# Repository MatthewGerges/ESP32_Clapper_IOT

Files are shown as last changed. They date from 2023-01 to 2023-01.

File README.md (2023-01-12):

# ESP32 Clapper Light - an IOT Project

 Video demo: https://www.youtube.com/watch?v=oGSny03s_TQ


- This project consists of an ESP32 microcontroller (programmed in C++)  that flips a light switch in 0.2 seconds upon detecting 2 claps
- I implemented it to an IOT framework by connecting it to a MongoDB database managed by NodeJS on the backend. The ESP32 will query for changes to the database every 0.5 seconds
- This project will soon have a React Native front end as well
- I also created a PCB that manages all the connections to the ESP32 and allows the circuit to be powered in 3 different ways (via a USB connection, a 3.7V battery connected to a boost converter that increases the voltage to 5V, and through a 12V DC barrel jack ran through a LM7805 converter with 2 capacitors to manage power ripples)
- The PCB was taken from start to finish - I did the schematic design - bought the parts off of digikey after creating a BOM and had it manufactured at JLC PCB after comparing pricing and quality of other PCB manufacturers
- Cases, enclosures and extensions were also created for this project on Fusion360 and printed on my personal Ender 3 V2 Printer (which took several iterations and rounds of prototyping)
 


This repo contains 4 folders: 
1) The ESP32 code written in C++
2) The backend code written in NodeJS which uses an MVC (model-view-controller) framework and will be connected to the front end of a React-Native app that is on the way of being built
3) The PCB designs - including all the files needed for manufacturing the PCB. It was created on Altium CircuitMaker. As such all the design documents can be viewed here: https://365.altium.com/files/E79B46BD-EABC-40B6-B3DB-7410488752D2
4) The Fusion360 3D designs (containing f3d - fusion360 design files- and STL files used to print the designs on my ender-3-V2 printer). These include several iterations of the PCB case, the servo motor extension and the pentagon-shaped knob extender for the light switch.

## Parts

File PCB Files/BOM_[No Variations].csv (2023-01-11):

Comment | Description | Designator | Footprint | LibRef | Quantity
TP4056 | Lithium Battery Charger |  | TP4056-Footprint-1 | CMP-88poo8h67ic0nqpqrd41-1 | 1
Battery Holder 18650 | Pcb Holder Thm 18650 Polarized | BT1 | PCB-nmv0vzhkfwsbxqx6kc1g-1 | CMP-40d98835f05c9f1e-4 | 1
Würth Elektronik 860010372006 | Aluminium Electrolytic Capacitor, WCAP-ATG8 Series, 100 F, 20%, 16 V, 5 mm, Radial Leaded | C1 | CAP-5x11-2 | CMP-7bd7b1e54b20a410-1 | 1
Würth Elektronik 860020374012 | Al Electrolytic Capacitors 470uF 16V | C2 | PCB-3azp1z6rt2bm1haulf0v-1 | CMP-e25928656d7f3d9e-1 | 1
DC Jack 5.5 2.1 | Conn; AV; Power; Jack; Mini; 2.0mmPinDia; RtAngle; Thru-hole; forS760, S765Plug | J1 | PCB-gxnxm3n04w37egsept5y-1 | CMP-da391331d91005fe-17 | 1
Sound Sensor HRS-1B-03-GA | Pin header, single-row 90° 3-pin [JST] S3B-XH-A Pin header, single-row 90° 3-pin | S1 | PCB-2zo40p8xruutr4eka9s5-1 | CMP-45008c3683009ac7-6 | 1
ServoMotor G800W305018EU | Pin header, single-row 90° 3-pin [JST] S3B-XH-A Pin header, single-row 90° 3-pin | S2 | PCB-2zo40p8xruutr4eka9s5-1 | CMP-45008c3683009ac7-6 | 1
Boost Converter | Pin header, single-row 90° 3-pin [JST] S3B-XH-A Pin header, single-row 90° 3-pin | S3 | PCB-2zo40p8xruutr4eka9s5-1 | CMP-45008c3683009ac7-6 | 1
E-Switch EG1218 | Slide Switch, 500 V, -20 to 70 degC, 3-Pin THD, RoHS | SW1 | ESWI-EG1218_V | CMP-9a5a5340a2f5459d-9 | 1
LM7805CT/NOPB | Linear Voltage Regulators 5 Volt Reg [Texas Instruments] | U1 | PCB-m217x3dwscnnq8k6ksmn-1 | CMP-8a9e42f854f65559-10 | 1
Espressif Systems ESP32-DEVKITC-32D with header | Eval Board For ESP-WROOM-32 - 38pin module with 8.4mm header | U2 | PCB-v7o6mlcnvy9ltvisia1k-2 | CMP-0991c5192c5ed656-39 | 1

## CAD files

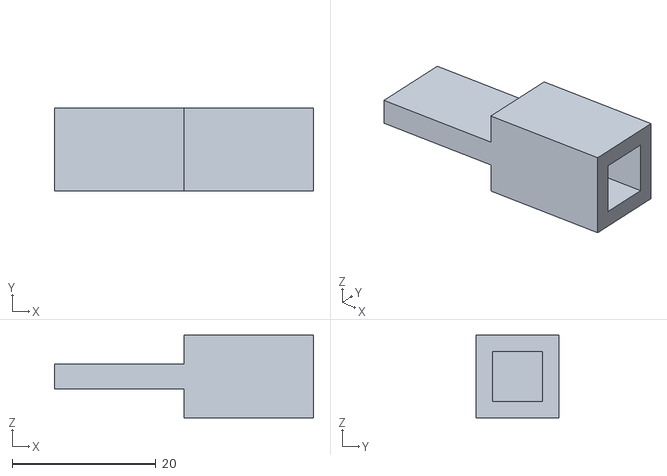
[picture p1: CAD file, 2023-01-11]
3D Design Files (Fusion360)/3D Print Files (STL)/KnobExt2_Brim.stl
36.0 x 11.5 x 11.5

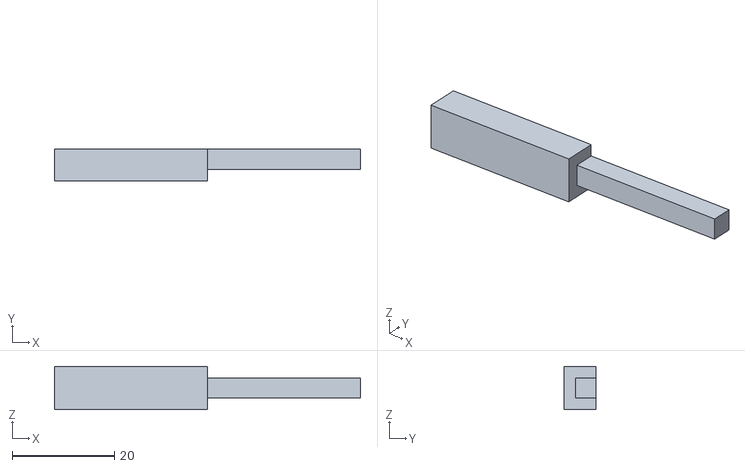
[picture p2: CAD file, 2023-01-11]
3D Design Files (Fusion360)/3D Print Files (STL)/ServoExtensionStraight_v2.stl
60.0 x 6.25 x 8.50

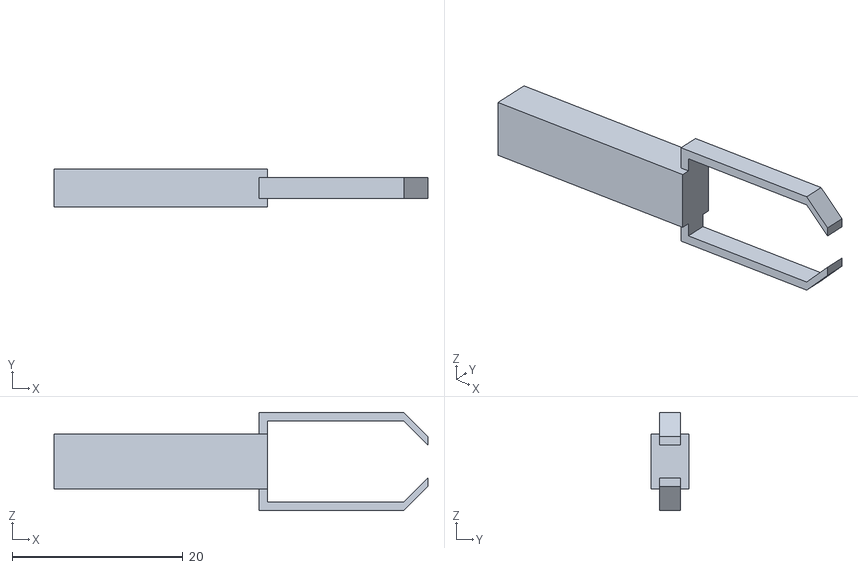
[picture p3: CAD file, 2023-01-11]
3D Design Files (Fusion360)/3D Print Files (STL)/Extension1.stl
43.8 x 4.50 x 11.5

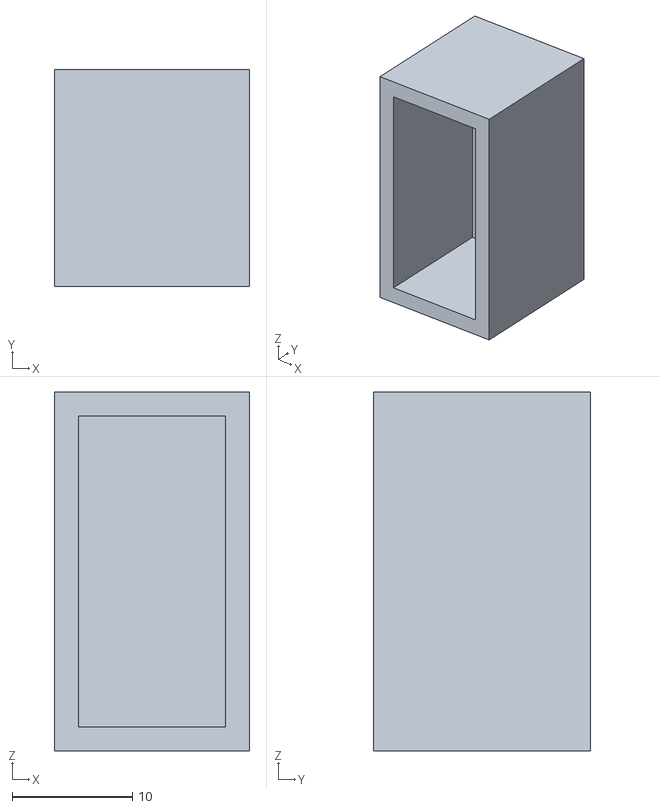
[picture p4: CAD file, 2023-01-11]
3D Design Files (Fusion360)/3D Print Files (STL)/ServoEncolosure2.stl
16.2 x 18.0 x 29.8

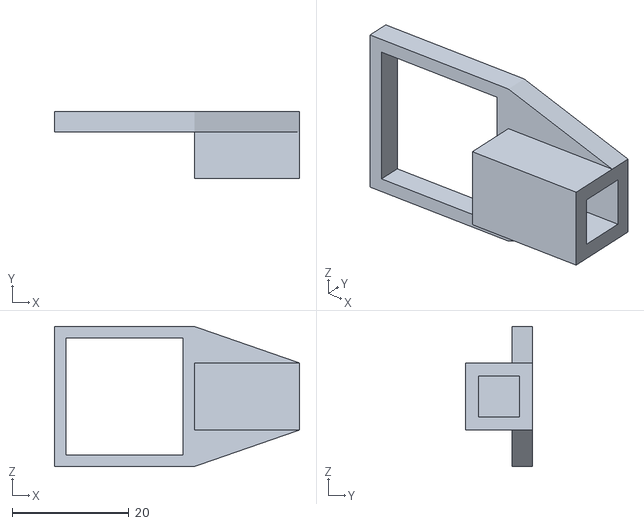
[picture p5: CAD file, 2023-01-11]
3D Design Files (Fusion360)/3D Print Files (STL)/KnobExtenderPentagon.stl
42.0 x 11.5 x 24.0

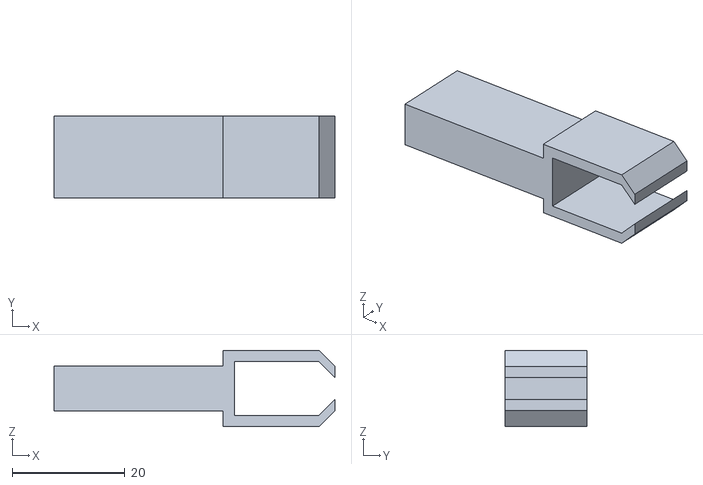
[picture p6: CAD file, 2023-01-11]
3D Design Files (Fusion360)/3D Print Files (STL)/Extension2.stl
49.8 x 14.5 x 13.5

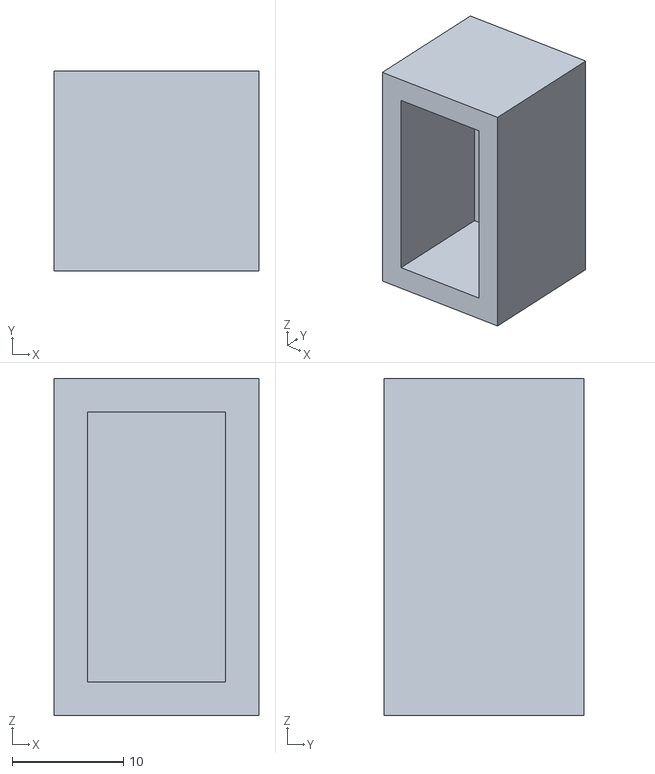
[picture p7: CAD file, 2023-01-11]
3D Design Files (Fusion360)/3D Print Files (STL)/ServoEncolosure1.stl
18.4 x 18.0 x 30.3

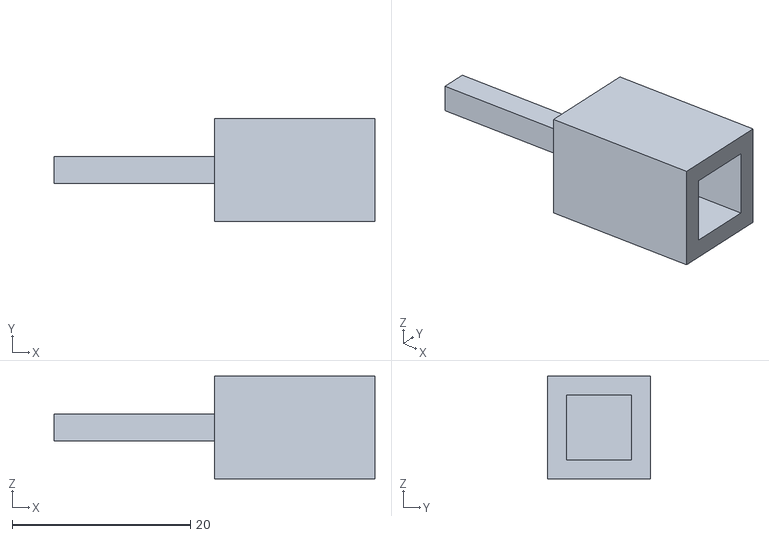
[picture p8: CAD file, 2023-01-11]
3D Design Files (Fusion360)/3D Print Files (STL)/KnobExtender1.stl
36.0 x 11.5 x 11.5

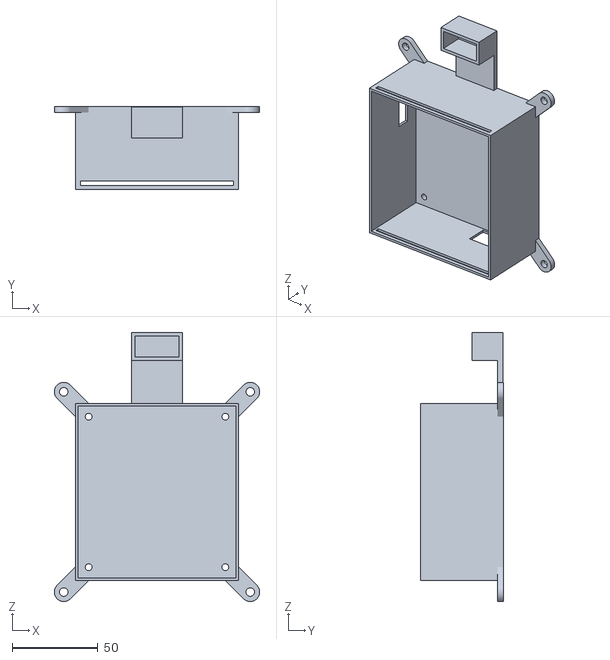
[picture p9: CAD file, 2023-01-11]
3D Design Files (Fusion360)/3D Print Files (STL)/PCBCase_v2_Slots.stl
119.5 x 48.5 x 156.4

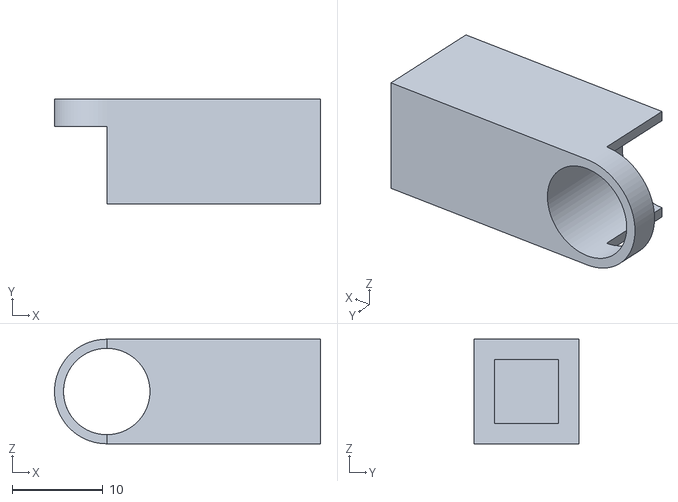
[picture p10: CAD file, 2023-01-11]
3D Design Files (Fusion360)/3D Print Files (STL)/KnobExtenderCircle.stl
29.2 x 11.5 x 11.5

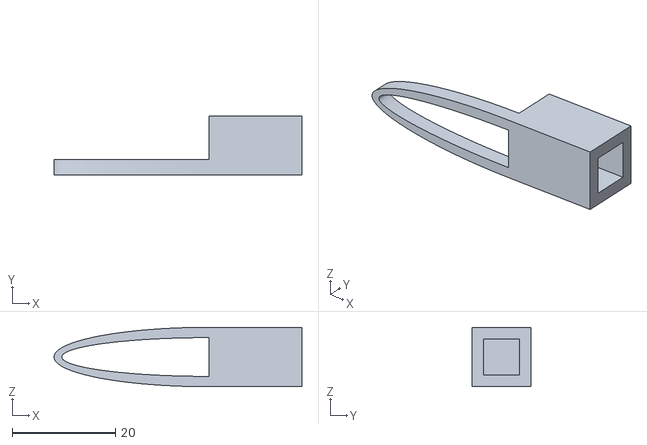
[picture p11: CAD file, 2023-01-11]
3D Design Files (Fusion360)/3D Print Files (STL)/KnobExtenderElipse.stl
48.0 x 11.5 x 11.5

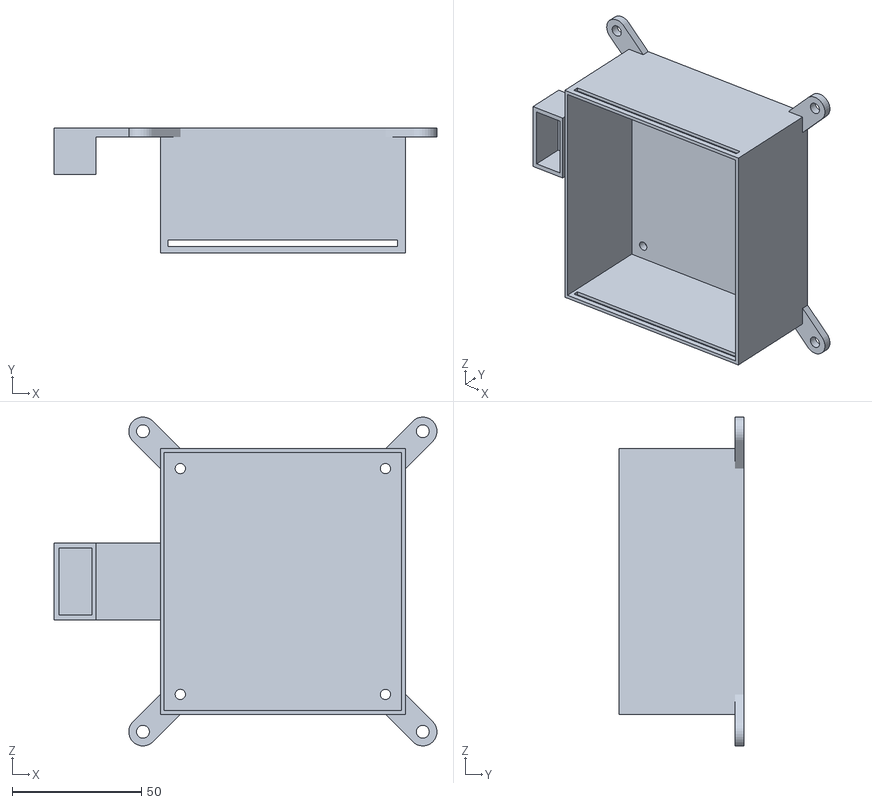
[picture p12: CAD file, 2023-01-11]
3D Design Files (Fusion360)/3D Print Files (STL)/PCBCase_v1_All.stl
148.4 x 48.5 x 127.5

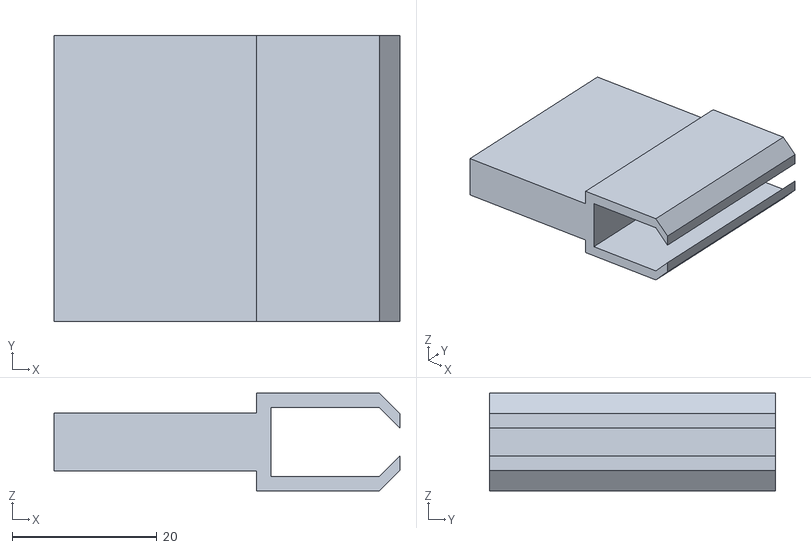
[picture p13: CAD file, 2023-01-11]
3D Design Files (Fusion360)/3D Print Files (STL)/Extension3.stl
47.8 x 39.5 x 13.5

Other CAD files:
3D Design Files (Fusion360)/3D Print Files (STL)/knobExtenderPentagon_2.stl
3D Design Files (Fusion360)/3D Print Files (STL)/PCBCase_v3_Aligned.stl
3D Design Files (Fusion360)/3D Print Files (STL)/ServoExtensionStraight.stl
3D Design Files (Fusion360)/Fusion360 Files (f3d)/LightKnobExtender.f3d
3D Design Files (Fusion360)/Fusion360 Files (f3d)/LightSwitcher.f3d
3D Design Files (Fusion360)/Fusion360 Files (f3d)/LightSwitcherStraight.f3d
3D Design Files (Fusion360)/Fusion360 Files (f3d)/PCBCase.f3d
3D Design Files (Fusion360)/Fusion360 Files (f3d)/ServoMotorEnclosure.f3d

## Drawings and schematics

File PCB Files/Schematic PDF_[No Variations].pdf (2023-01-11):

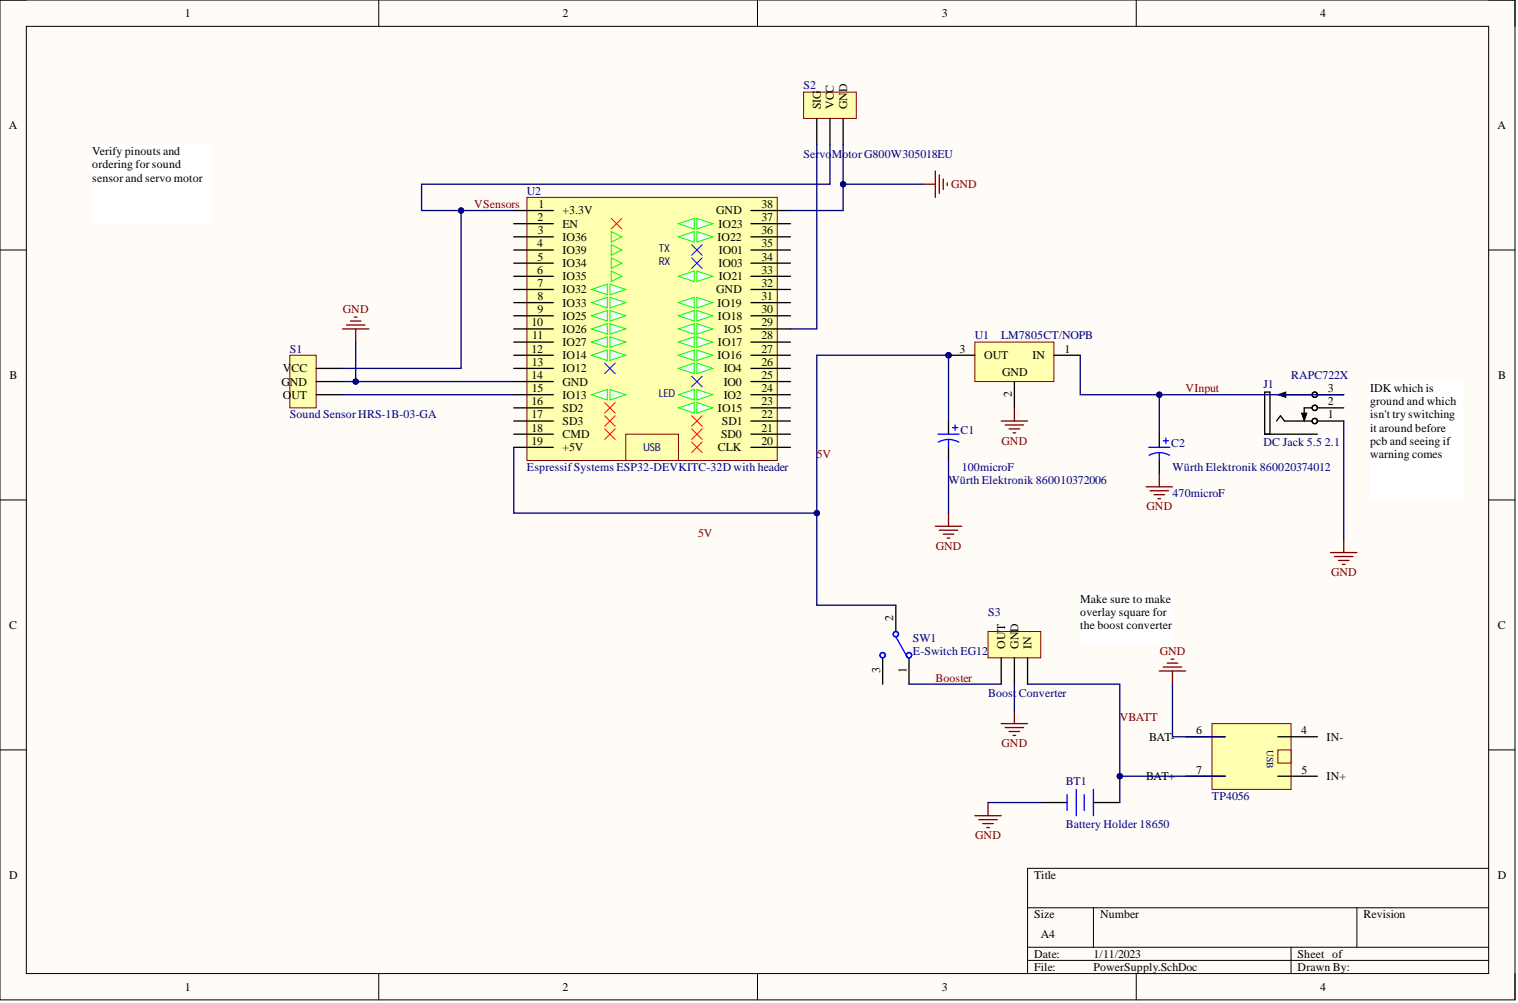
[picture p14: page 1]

Verify pinouts and
ordering for sound
sensor and servo motor

IDK which is
ground and which
isn't try switching
it around before
pcb and seeing if
warning comes

Espressif Systems ESP32-DEVKITC-32D with header

Make sure to make
overlay square for
the boost converter

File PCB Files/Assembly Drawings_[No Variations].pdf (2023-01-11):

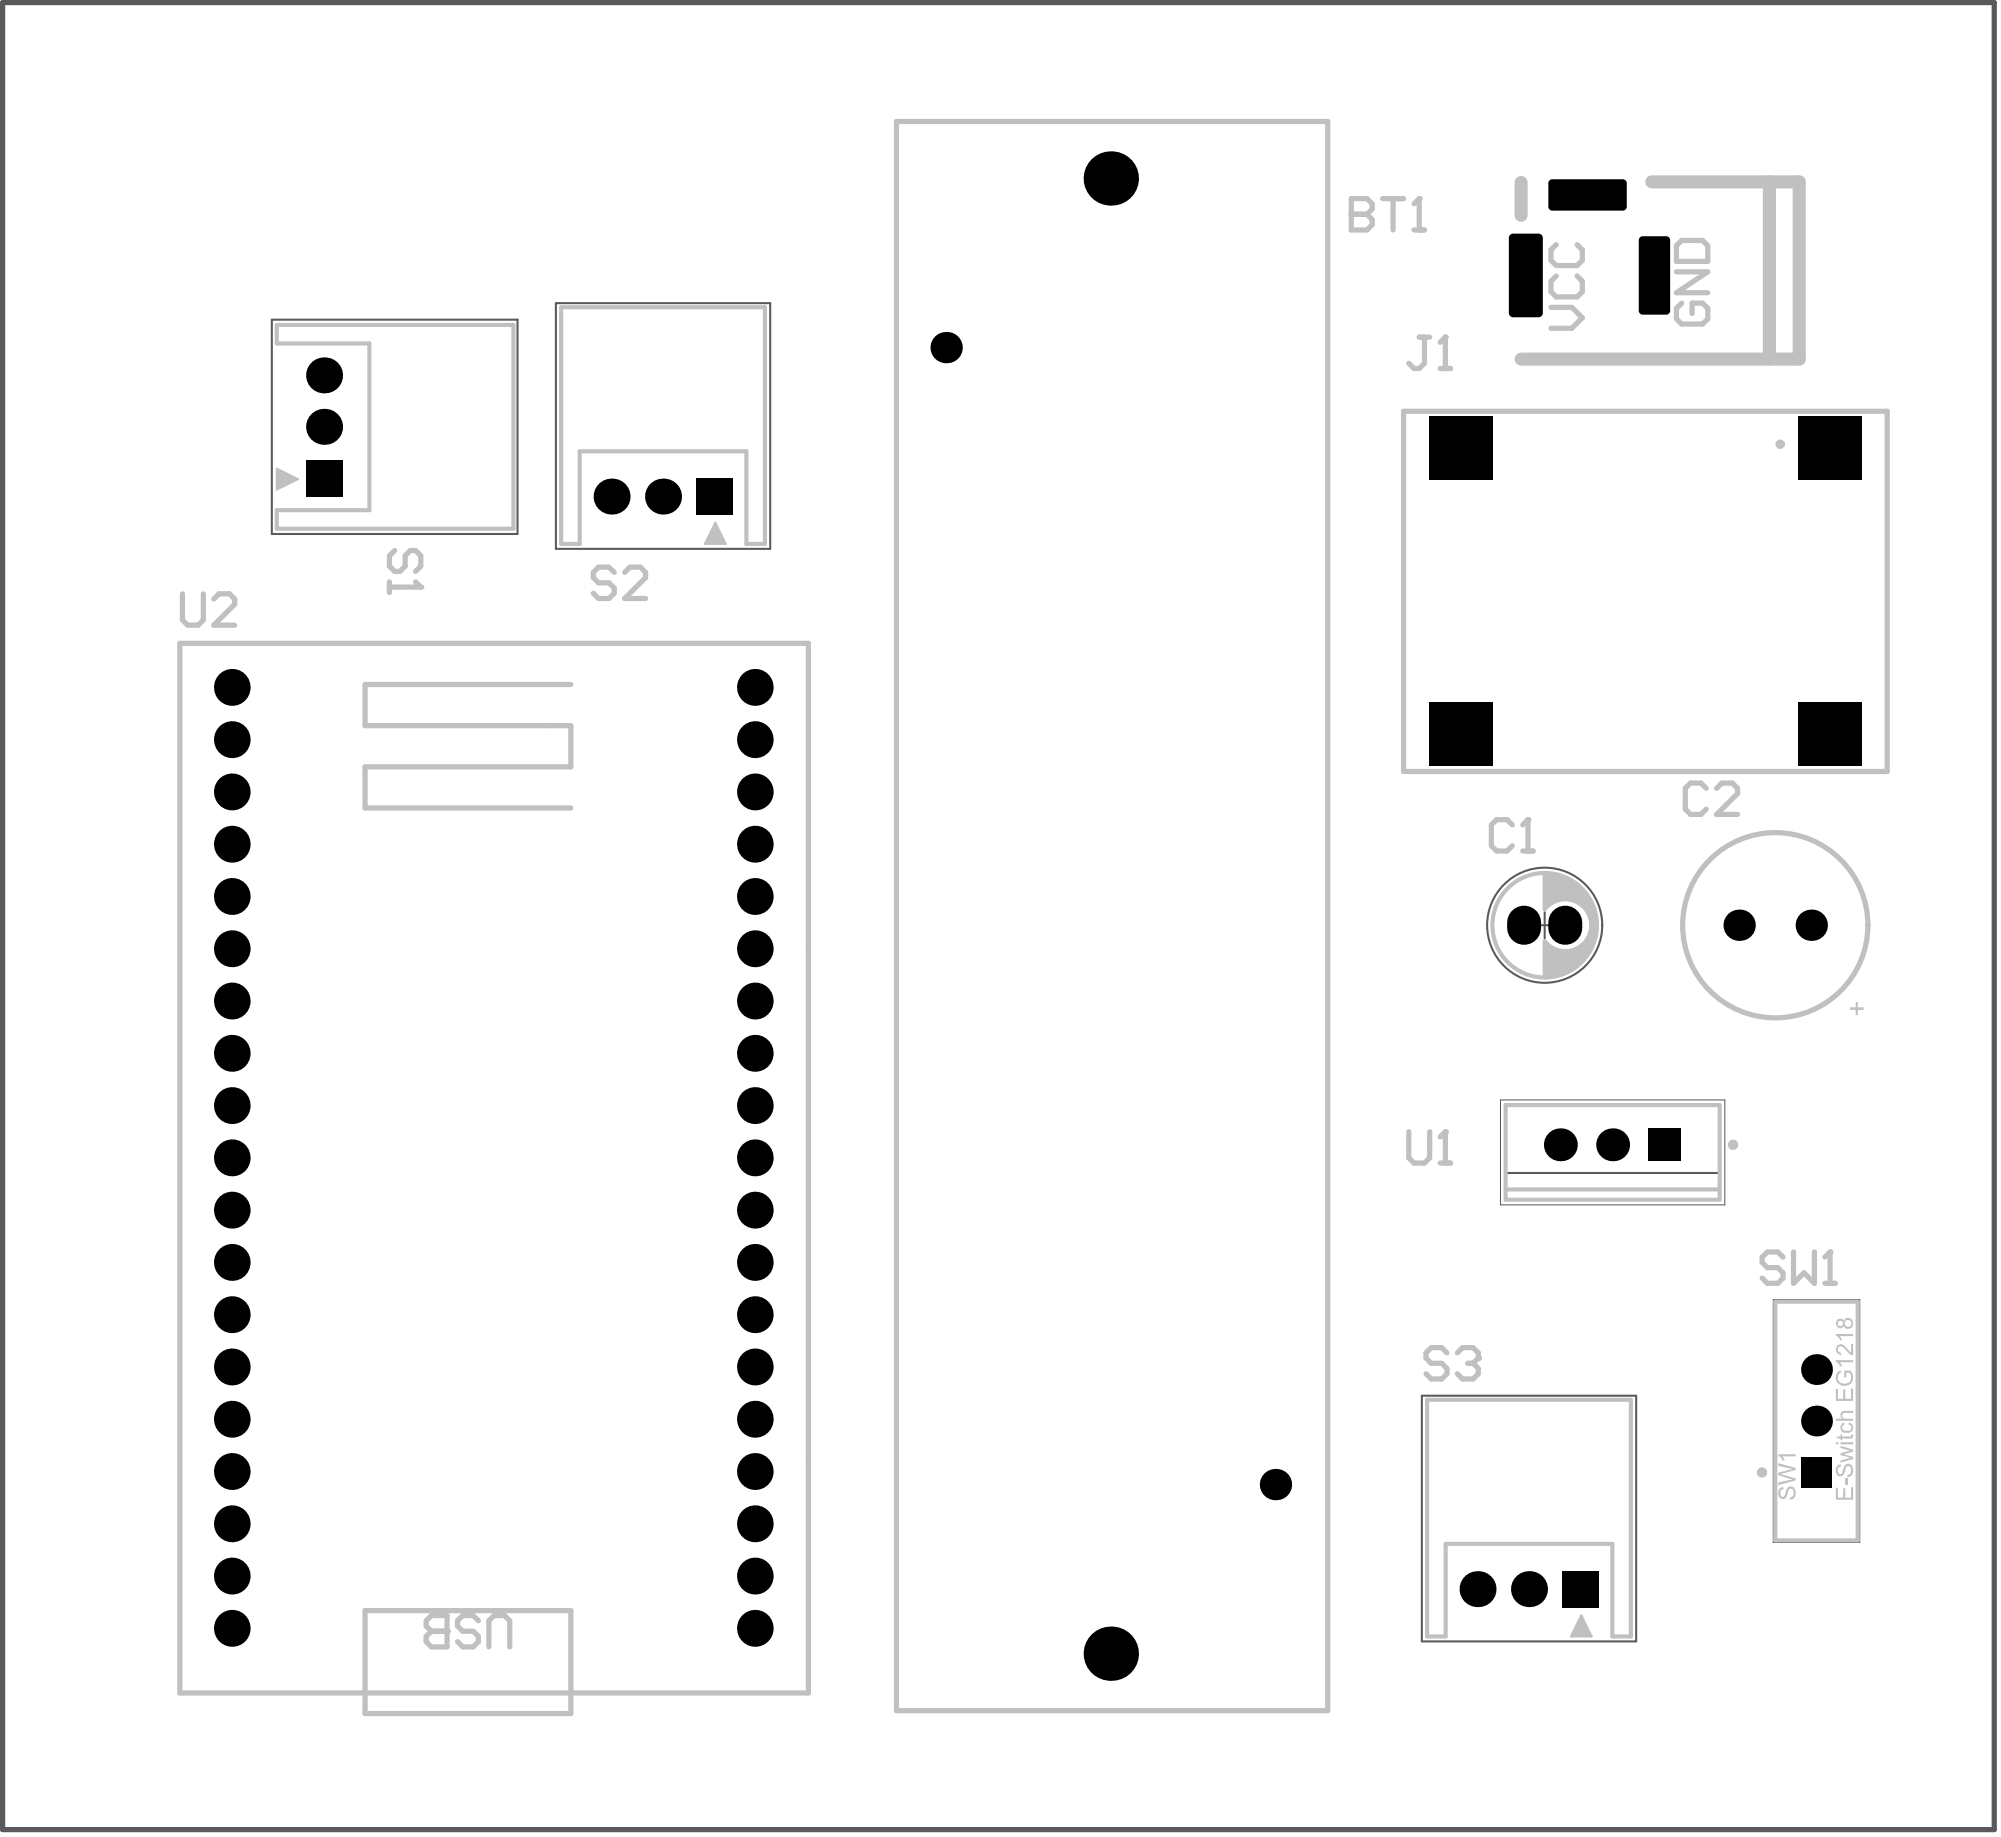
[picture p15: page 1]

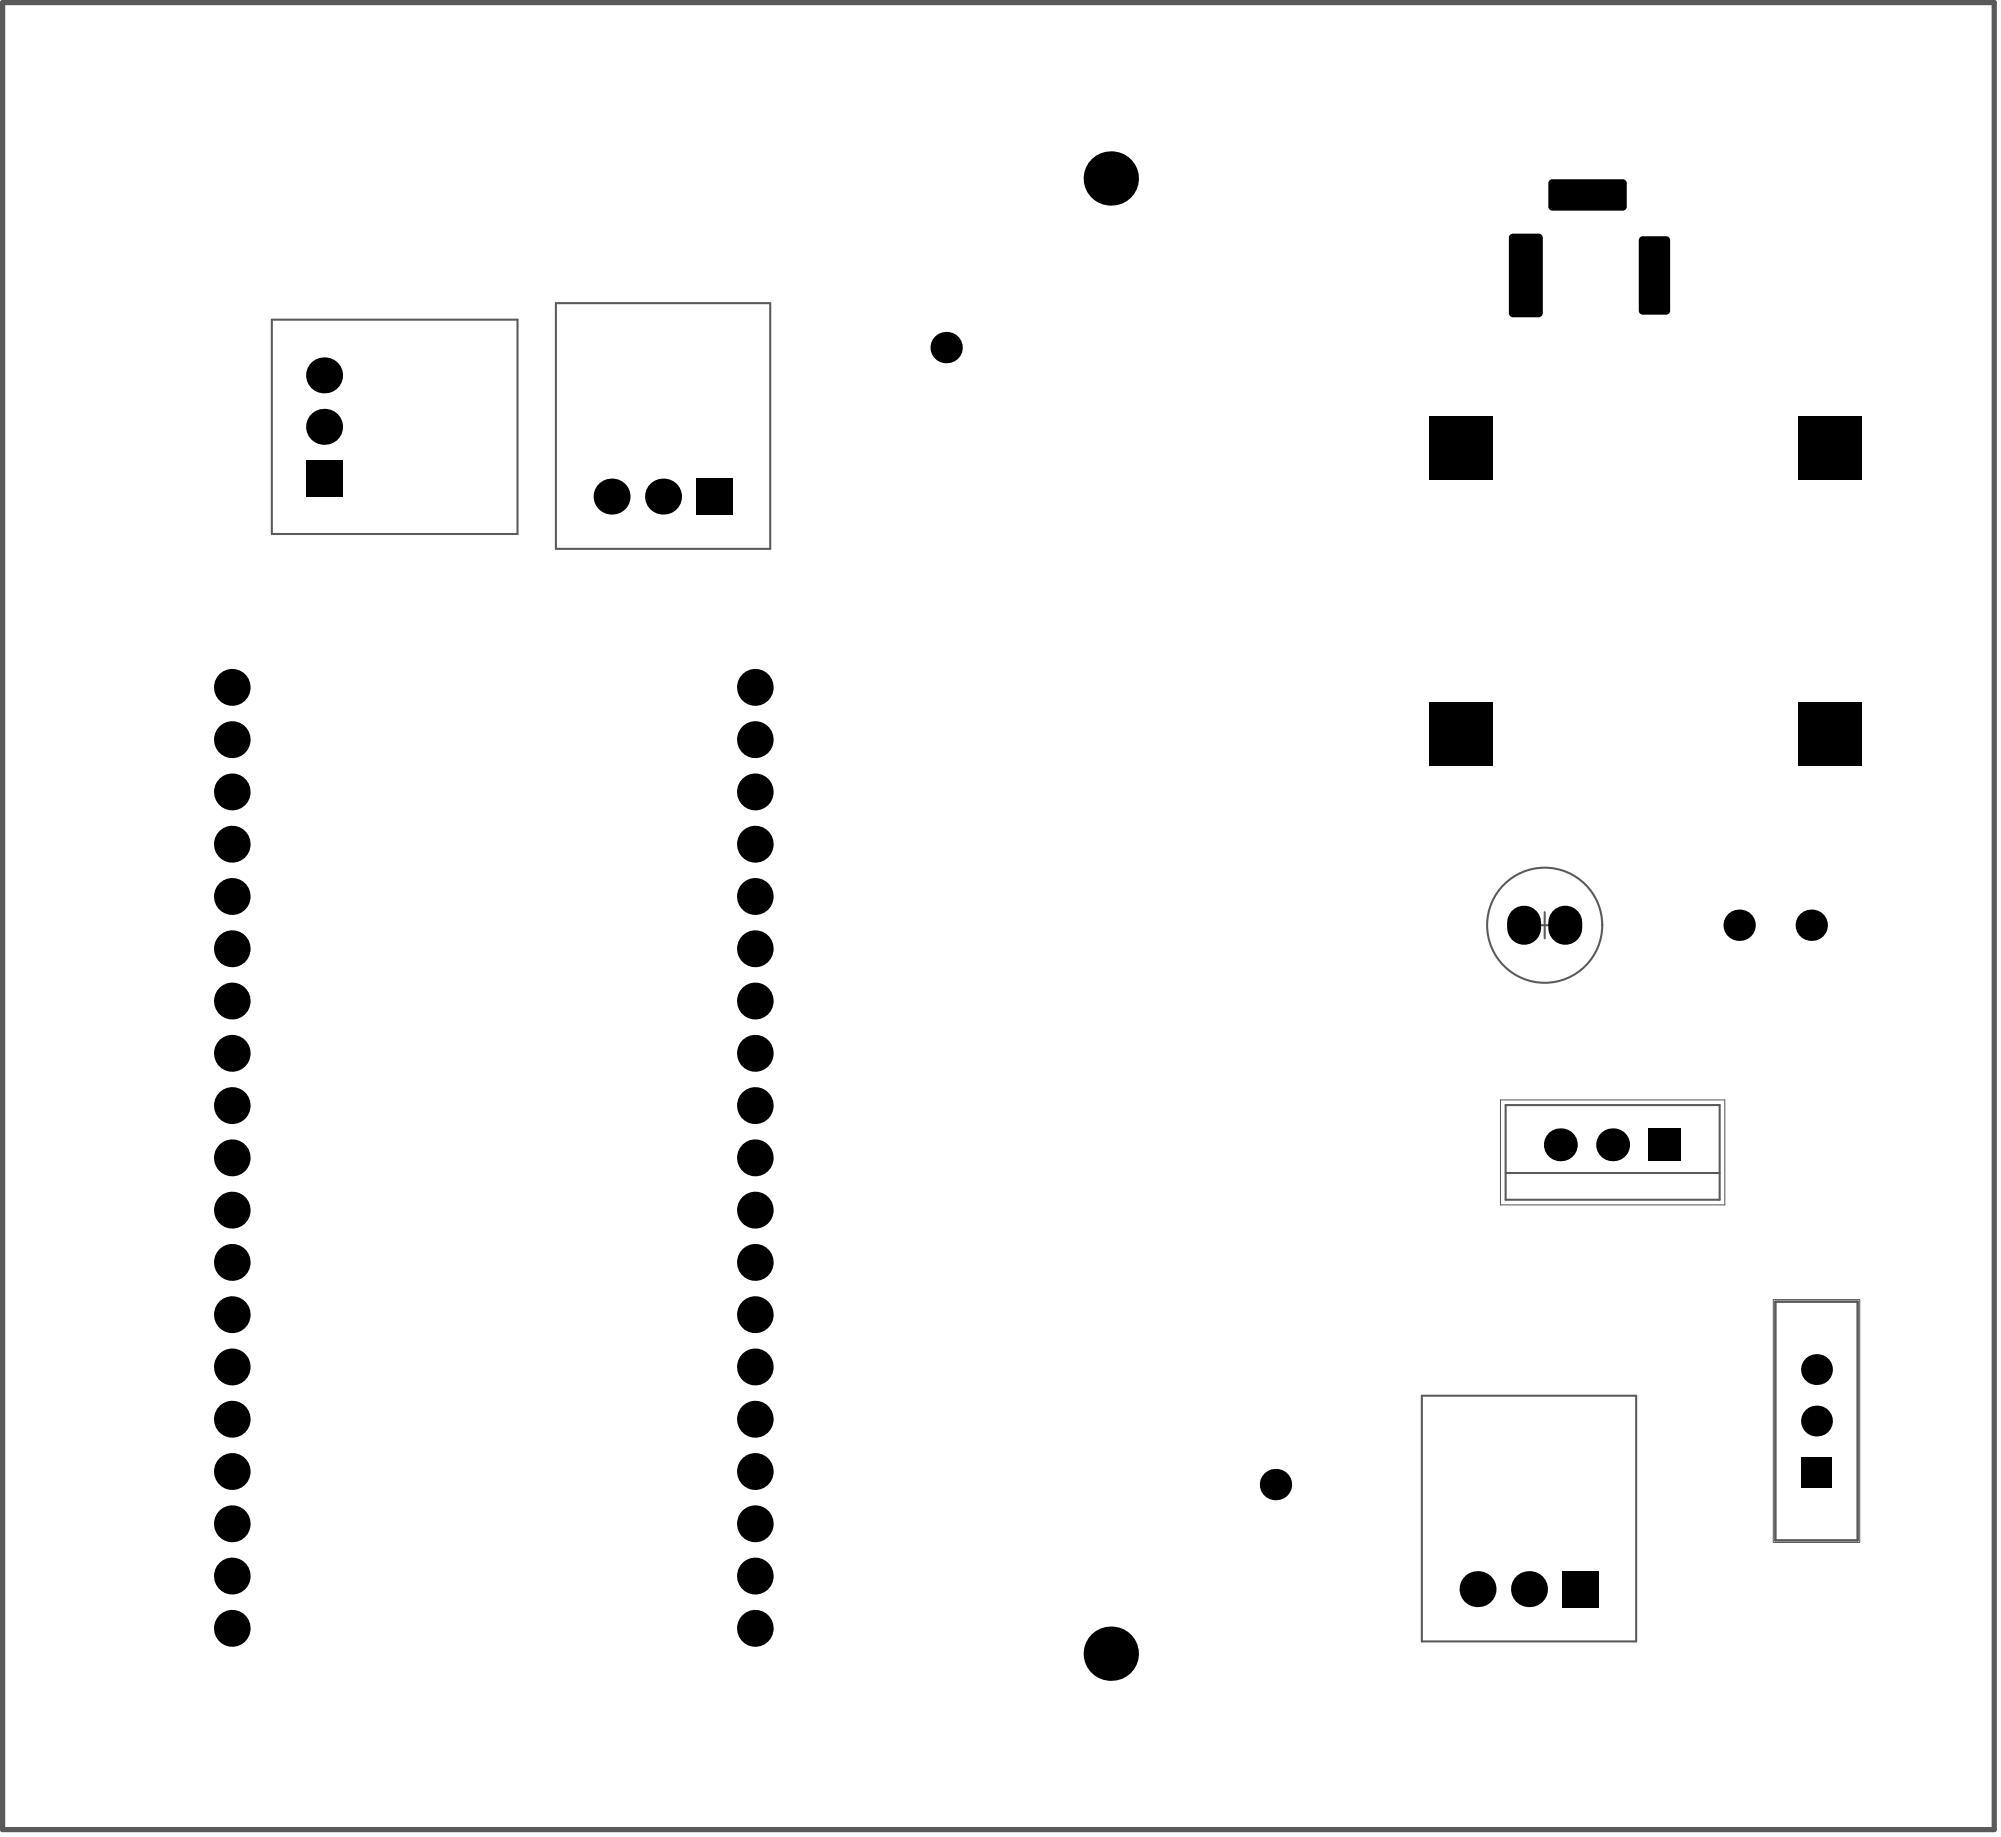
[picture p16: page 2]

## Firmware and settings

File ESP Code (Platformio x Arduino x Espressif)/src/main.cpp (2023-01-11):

/*
 * Blink
 * Turns on an LED on for one second,
 * then off for one second, repeatedly.
 */

#include <Arduino.h>
//#include <ESP32_Servo.h>
#include "ESP32Servo.h"
#include <WiFi.h>
#include <ESPmDNS.h>
#include <WiFiUdp.h>
#include <ArduinoOTA.h>


// Set LED_BUILTIN if it is not defined by Arduino framework
#ifndef LED_BUILTIN
    #define LED_BUILTIN 2
#endif
#define PIN_SERVO 5
#define MIC_OUT_PIN 13
Servo myServo;
const char* ssid = "Jojofofa";
const char* password = "Fofafofa";

int micPin = 32;
int micPinDigital = 3;
int sensorValue = 0;
int digitalState = 0;


int mic = 13;
int indicLED = 9;
int lightPin = 2;
bool lightState = true;
bool ignoreInt = false;
bool clapDetected = false;
uint32_t ClapDetectedTime[3]{};
void ISR_ClapDetected();

void setup() {
  //Serial.begin(115200);
  pinMode(indicLED, OUTPUT);
  pinMode(lightPin, OUTPUT);
  digitalWrite(lightPin, lightState);
  attachInterrupt(digitalPinToInterrupt(mic), ISR_ClapDetected, FALLING);
  
  //pinMode(LED_BUILTIN, OUTPUT);
  pinMode(micPinDigital, INPUT);
  myServo.attach(PIN_SERVO);
  myServo.write(110);
  Serial.begin(115200);
  Serial.println("Booting");

}

void loop() {
  // myServo.write(150);
  // delay(500);
  // myServo.write(50);
  // delay(500);

  delay(2);

  if (millis() - ClapDetectedTime[2] >= 800)
  {
    digitalWrite(indicLED, LOW);
  }
  if (millis() - ClapDetectedTime[2] < 800 && millis() - ClapDetectedTime[1] < 800 && clapDetected && ClapDetectedTime[1] - ClapDetectedTime[0 >= 800])
  {
    Serial.println("double clap detected");
    digitalWrite(indicLED, LOW);
    Serial.print("Setting light to");
    Serial.println(String(!lightState));

    if(lightState)
  {
    myServo.write(105);
  }
  else{
  //delay(1000);
  myServo.write(135);
  }
    digitalWrite(lightPin, lightState);

    delay(820);
    lightState = !lightState;
    clapDetected = false;
  }

}

void ISR_ClapDetected()
{
  if(millis() - ClapDetectedTime[2] > 200)
  {
    for (int i = 0; i != 2; i++)
    {
      ClapDetectedTime[i] = ClapDetectedTime[i + 1];
    }

    ClapDetectedTime[2] = millis();
    clapDetected = true;
    Serial.println("clap detected");
    digitalWrite(indicLED, HIGH);
  }
}



// void setup()
// {
//   // initialize LED digital pin as an output.
//   pinMode(LED_BUILTIN, OUTPUT);
//   pinMode(micPinDigital, INPUT);
//   myServo.attach(PIN_SERVO);
//   Serial.begin(115200);
//   Serial.println("Booting");
//   #if WIFI
//   WiFi.mode(WIFI_STA);
//   WiFi.begin(ssid, password);
//   while (WiFi.waitForConnectResult() != WL_CONNECTED) {
//     Serial.println("Connection Failed! Rebooting...");
//     delay(5000);
//     ESP.restart();
//   }

//   // Port defaults to 3232
//   // ArduinoOTA.setPort(3232);

//   // Hostname defaults to esp3232-[MAC]
//   // ArduinoOTA.setHostname("myesp32");

//   // No authentication by default
//   // ArduinoOTA.setPassword("admin");

//   // Password can be set with it's md5 value as well
//   // MD5(admin) = 21232f297a57a5a743894a0e4a801fc3
//   // ArduinoOTA.setPasswordHash("21232f297a57a5a743894a0e4a801fc3");

//   ArduinoOTA
//     .onStart([]() {
//       String type;
//       if (ArduinoOTA.getCommand() == U_FLASH)
//         type = "sketch";
//       else // U_SPIFFS
//         type = "filesystem";

//       // NOTE: if updating SPIFFS this would be the place to unmount SPIFFS using SPIFFS.end()
//       Serial.println("Start updating " + type);
//     })
//     .onEnd([]() {
//       Serial.println("\nEnd");
//     })
//     .onProgress([](unsigned int progress, unsigned int total) {
//       Serial.printf("Progress: %u%%\r", (progress / (total / 100)));
//     })
//     .onError([](ota_error_t error) {
//       Serial.printf("Error[%u]: ", error);
//       if (error == OTA_AUTH_ERROR) Serial.println("Auth Failed");
//       else if (error == OTA_BEGIN_ERROR) Serial.println("Begin Failed");
//       else if (error == OTA_CONNECT_ERROR) Serial.println("Connect Failed");
//       else if (error == OTA_RECEIVE_ERROR) Serial.println("Receive Failed");
//       else if (error == OTA_END_ERROR) Serial.println("End Failed");
//     });

//   ArduinoOTA.begin();

//   Serial.println("Ready");
//   Serial.print("IP address: ");
//   Serial.println(WiFi.localIP());
//   #endif
// }

// int delayTime = 100;

// void loop()
// {
//   #if WIFI
//   ArduinoOTA.handle();  
//   #endif
//   // turn the LED on (HIGH is the voltage level)
//   digitalWrite(LED_BUILTIN, HIGH);
//   // wait for a second
//   delay(delayTime);
//   // turn the LED off by making the voltage LOW
//   digitalWrite(LED_BUILTIN, LOW);
//    // wait for a second
//   delay(delayTime);

//   // for (int pos = 0; pos <= 300; pos += 20)
//   // {
//   //   myServo.write(pos);
//   //   delay(500);
//   // }

//   // for (int i = 0; i < 10; i++)
//   // {
//   //   myServo.write(100);
//   //   delay(3000);
//   //   myServo.write(120);
//   //   delay(3000);
//   // }

//   myServo.write(170);
//   delay(1000);
//   myServo.write(20);
  
//   #ifdef WIFI
//   sensorValue = analogRead(micPin);
//   digitalState = digitalRead(micPinDigital);
//   Serial.println(sensorValue, DEC);
//   Serial.println(digitalState);
//   delay(500);

//   Serial.println(digitalRead(MIC_OUT_PIN));
//   #endif

  
  
// }

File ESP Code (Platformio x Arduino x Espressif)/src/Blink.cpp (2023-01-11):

// /* Blink Example
//    This example code is in the Public Domain (or CC0 licensed, at your option.)
//    Unless required by applicable law or agreed to in writing, this
//    software is distributed on an "AS IS" BASIS, WITHOUT WARRANTIES OR
//    CONDITIONS OF ANY KIND, either express or implied.
// */

// #include <stdio.h>
// #include <freertos/FreeRTOS.h>
// #include <freertos/task.h>
// #include <driver/gpio.h>
// #include "sdkconfig.h"
// #include <Arduino.h>

// /* Can run 'make menuconfig' to choose the GPIO to blink,
//    or you can edit the following line and set a number here.
// */
// #define BLINK_GPIO (gpio_num_t)CONFIG_BLINK_GPIO

// #ifndef LED_BUILTIN
// #define LED_BUILTIN 4
// #endif

// void blink_task(void *pvParameter)
// {
//     /* Configure the IOMUX register for pad BLINK_GPIO (some pads are
//        muxed to GPIO on reset already, but some default to other
//        functions and need to be switched to GPIO. Consult the
//        Technical Reference for a list of pads and their default
//        functions.)
//     */
//     gpio_pad_select_gpio(BLINK_GPIO);
//     /* Set the GPIO as a push/pull output */
//     gpio_set_direction(BLINK_GPIO, GPIO_MODE_OUTPUT);
//     while(1) {
//         /* Blink off (output low) */
//         gpio_set_level(BLINK_GPIO, 0);
//         vTaskDelay(1000 / portTICK_PERIOD_MS);
//         /* Blink on (output high) */
//         gpio_set_level(BLINK_GPIO, 1);
//         vTaskDelay(1000 / portTICK_PERIOD_MS);
//     }
// }

// #if !CONFIG_AUTOSTART_ARDUINO
// void arduinoTask(void *pvParameter) {
//     pinMode(LED_BUILTIN, OUTPUT);
//     while(1) {
//         digitalWrite(LED_BUILTIN, !digitalRead(LED_BUILTIN));
//         delay(1000);
//     }
// }

// extern "C" void app_main()
// {
//     // initialize arduino library before we start the tasks
//     initArduino();

//     xTaskCreate(&blink_task, "blink_task", configMINIMAL_STACK_SIZE, NULL, 5, NULL);
//     xTaskCreate(&arduinoTask, "arduino_task", configMINIMAL_STACK_SIZE, NULL, 5, NULL);
// }
// #else
// void setup() {
//     Serial.begin(115200);
//     xTaskCreate(&blink_task, "blink_task", configMINIMAL_STACK_SIZE, NULL, 5, NULL);
//     pinMode(LED_BUILTIN, OUTPUT);
// }
// void loop() {
//     digitalWrite(LED_BUILTIN, !digitalRead(LED_BUILTIN));
//     Serial.println("Hello!");
//     delay(1000);
//     ESP_LOGI("COOL STUFF", "it's going well fingers crossed");
// }
// #endif
